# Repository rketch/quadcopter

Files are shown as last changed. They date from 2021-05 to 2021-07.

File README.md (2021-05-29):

# When Pigs Fly: The Quadcopter Project
The hardware and firmware for a quadcopter were made in the UCSD class CSE 176e: Robotic System Design and Implementation with [@ThomasStuart](https://github.com/ThomasStuart)

## Video of the quadcopter (click on gif)
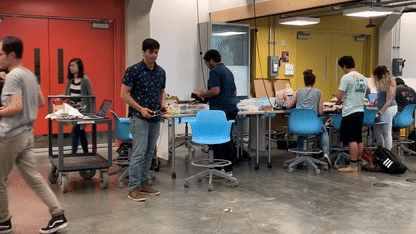
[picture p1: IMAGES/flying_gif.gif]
flying gif (https://www.youtube.com/watch?v=QjpneSxLLBc)


## Report on the design process
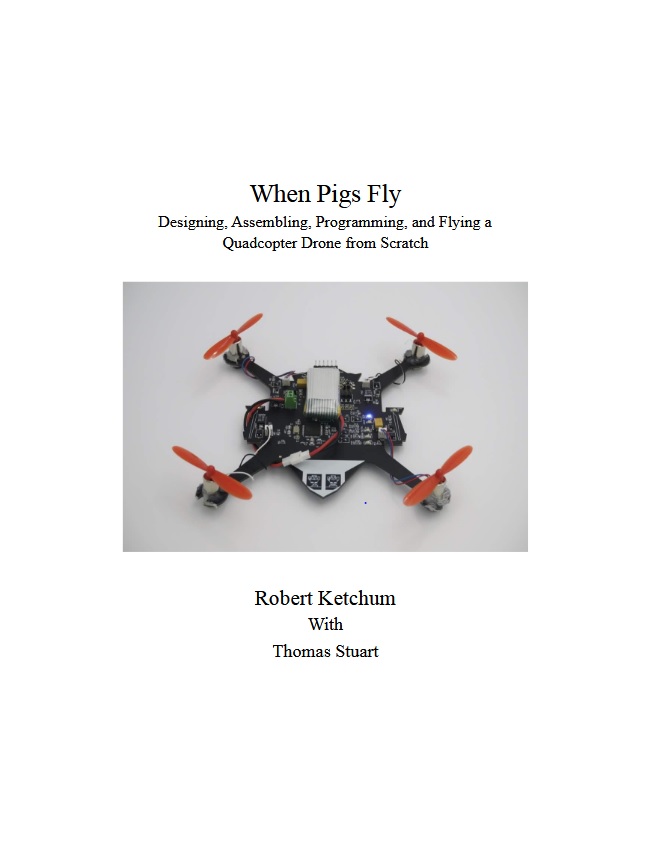
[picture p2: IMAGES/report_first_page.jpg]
photoshoot picture


## Various Pictures

Assembled quadcopter
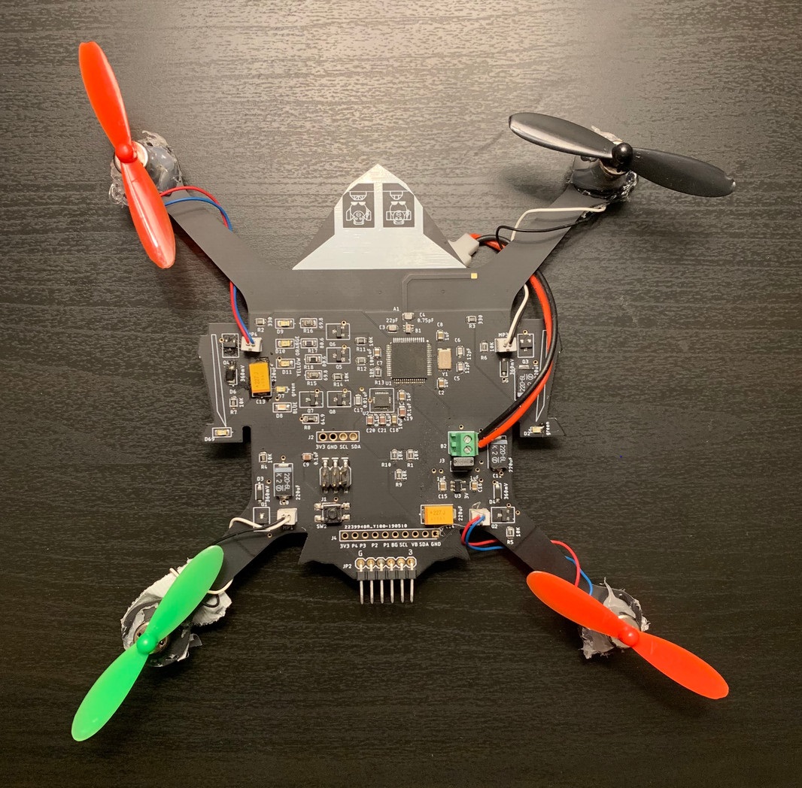
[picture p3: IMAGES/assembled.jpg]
assembled


Four bladed propellers with IMU breakout board
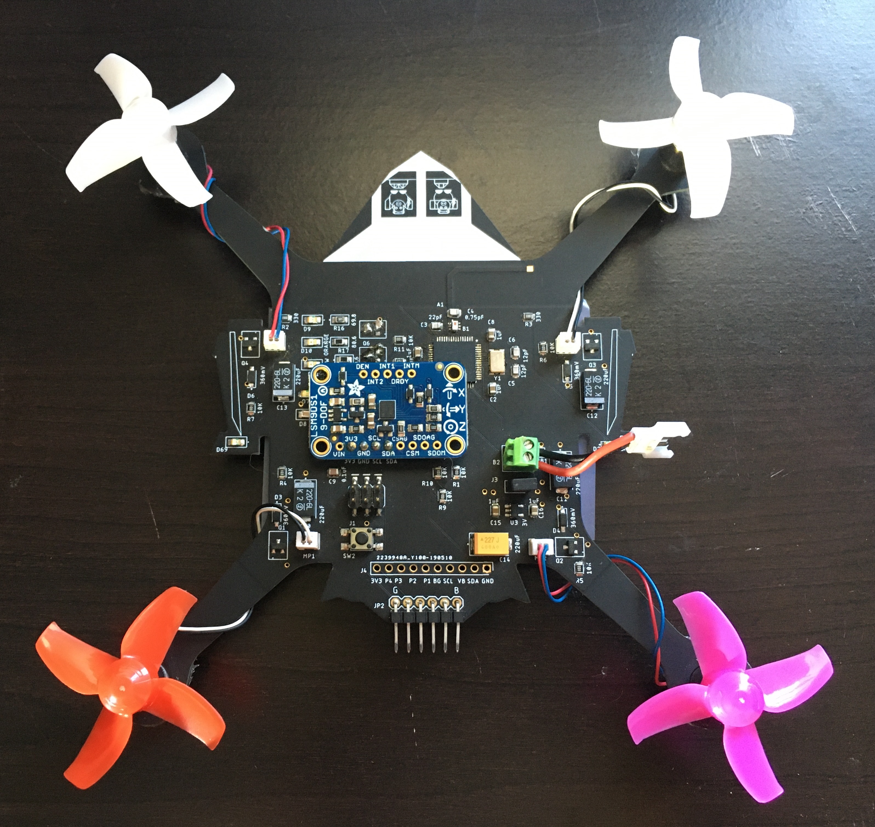
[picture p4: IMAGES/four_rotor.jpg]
four rotor


Remote PID control system tuning menu
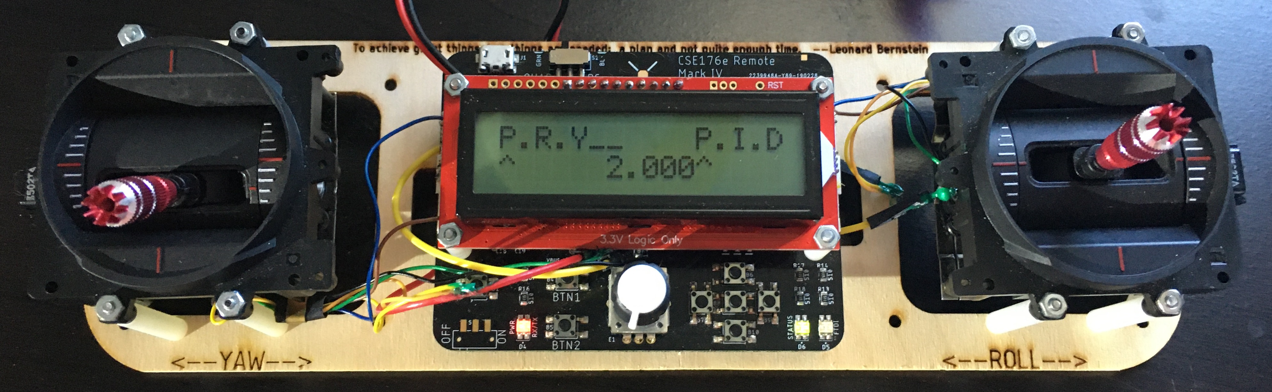
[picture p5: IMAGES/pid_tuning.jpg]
remote PID


Remote trim tuning menu
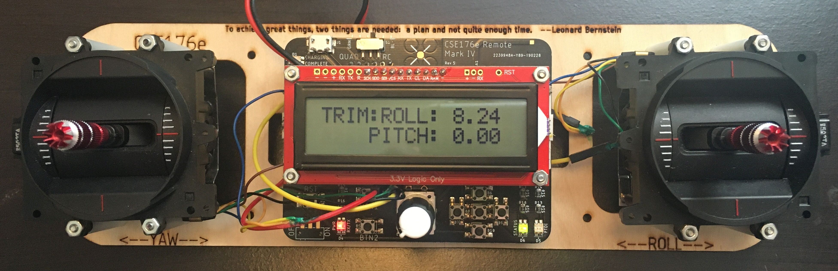
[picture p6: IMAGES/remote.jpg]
remote trim


Quadcopter orientation angles
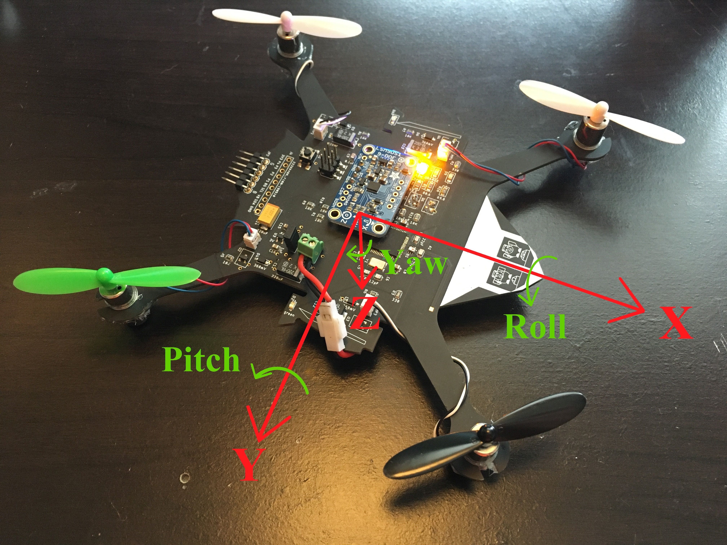
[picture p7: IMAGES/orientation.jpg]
orientation


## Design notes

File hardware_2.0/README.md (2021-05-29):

# EAGLE schematic and Board Files
These were updated in version 2.0 to fix wiring issues from the rainbow LED FETs to the microcontroller pins.

Created by @rketch and @ThomasStuart with continued updates and revisions by @rketch.

Libraries created by @stevenjswanson.

## Schematic
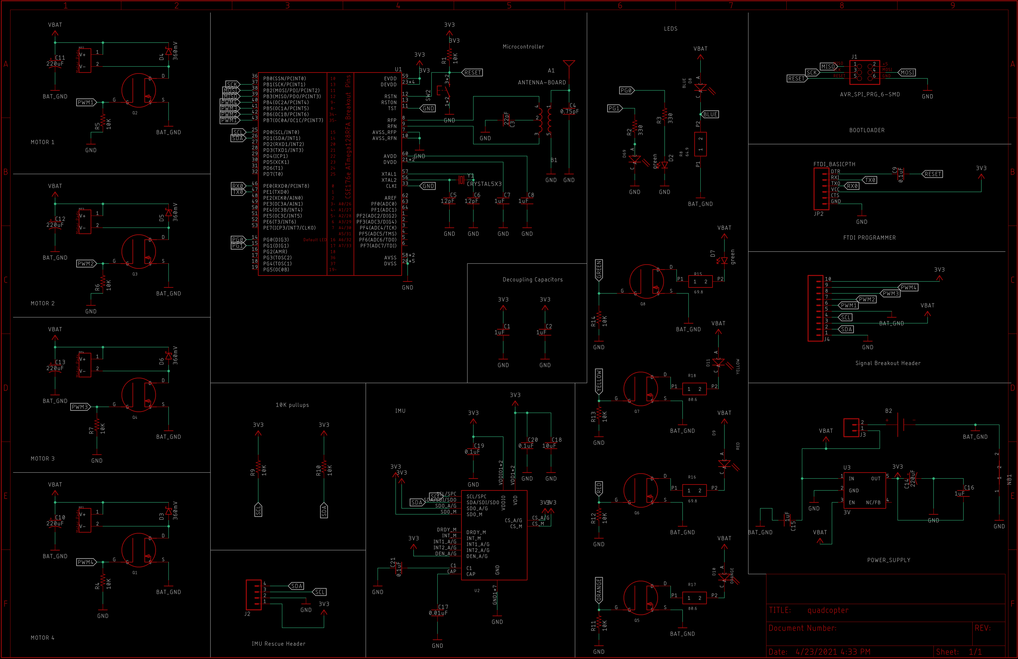
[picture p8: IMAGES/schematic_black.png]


## Layout
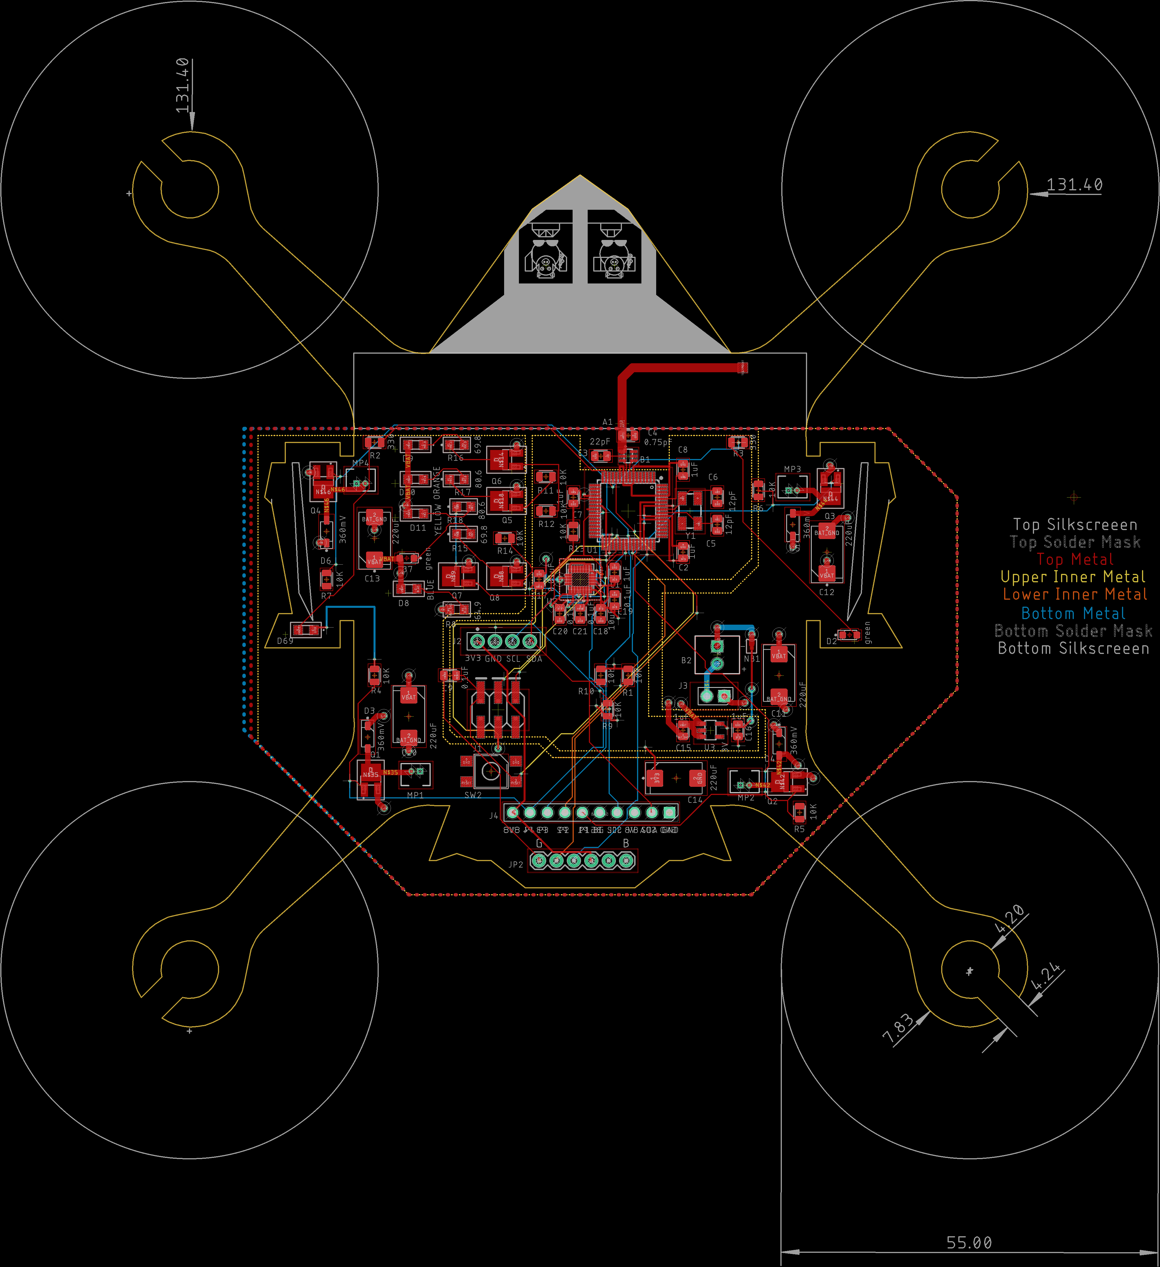
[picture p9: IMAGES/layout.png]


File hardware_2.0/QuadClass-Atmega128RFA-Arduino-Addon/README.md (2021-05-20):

# Arduino Board definitions for the ATmega128RFA1-based boards

This folder should be added to a *hardware* directory within your Arduino sketchbook. Normally the sketchbook will install to your documents/Arduino folder. If a *hardware* folder isn't already there, make it.

This directory contains a *boards.txt* file which defines how Arduino will handle ATmega128RFA1-based boards for the Quadcopter Class, and adds a selectable option under the *Tools > Board* menu. When you open the Arduino ID (close and reopen if it's already open), this option should be added to the menu.

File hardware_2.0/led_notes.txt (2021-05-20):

We have a total of 5 added LEDs.

Our blue LED D8 will be powered by the battery at 4.2 V. It is always on.
forward voltage: 2.9 V
Current limiting resistor: 64.9 ohms
LED current: 0.02 A

Our green LED D7 will be powered by the battery at 4.2 V. It wired to a MOSFET to blink at a programmed throttle position.
forward voltage: 2.1 V
Current limiting resistor: 69.8 ohms
LED current: 0.03 A

Our yellow LED D11 will be powered by the battery at 4.2 V. It wired to a MOSFET to blink at a programmed throttle position.
forward voltage: 1.85 V
Current limiting resistor: 80.6 ohms
LED current: 0.029 A

Our orange LED D10 will be powered by the battery at 4.2 V. It wired to a MOSFET to blink at a programmed throttle position.
forward voltage: 1.8 V
Current limiting resistor: 80.6 ohms
LED current: 0.03 A

Our red LED D9 will be powered by the battery at 4.2 V. It wired to a MOSFET to blink at a programmed throttle position.
forward voltage: 2.0 V
Current limiting resistor: 69.8 ohms
LED current: 0.032 A

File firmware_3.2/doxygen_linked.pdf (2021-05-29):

## Quadcopter

3.2

Generated by Doxygen 1.8.16

i

1 Quadcopter | 1
2 File Index | 3
3 File Documentation | 5

Generated by Doxygen

ii

iii

Index | 27

# Chapter 1

# Quadcopter

## 1.1 Description

The C++ Arduino firmware for a quadcopter made as part of UCSD class CSE 176e

## 1.2 Hardware

Custom PCB utilizing the ATmega128RFA1.

- Quadcopter hardware by Thomas Stuart and Robert Ketchum. Documentation and EAGLE board files available here: https://github.com/rketch/quadcopter
- Remote PCB made by UCSD Professor Steven Swanson.

## 1.3 Libraries

All libraries available at: https://github.com/rketch/quadcopter

- Wire

– Arduino I2C

- Arduino_LSM9DS1

– Onboard IMU for quadcopter orientation.

- Adafruit_Simple_AHRS

– Attitude and heading reference system for LSM

- radio

– Radio library. Modified to include data structure sent via radio

- quad_remote

– Custom CSE 176e library for the remote

- EEPROM

– To save PID and trim calibration values to Non-volatile memory

- RotaryEncoder

– To use the knob and button

### 2 Quadcopter

## 1.4 Authors

Created by Thomas Stuart and Robert Ketchum, April 2019. Modified by Robert Ketchum, May 2021.

# Chapter 2

# File Index

## 2.1 File List

Here is a list of all files with brief descriptions:

### 4 File Index

# Chapter 3

# File Documentation

## 3.1 quad_firmware/quad_firmware.ino File Reference

#include "radio.h"

#include <Wire.h>

#include <Adafruit_Simple_AHRS.h> #include <Adafruit_LSM9DS1.h>

Macros

- #define RADIO_CH 17

Radio Channel.
- #define M1 35

Pin 35 is mapped to motor 1.
- #define M2 34

Pin 34 is mapped to motor 2.
- #define M3 8

Pin 8 is mapped to motor 3.
- #define M4 9

Pin 9 is mapped to motor 4.
- #define FILT_RATIO 0.91

Complementary filter ratio for a time constant of 10 Hz = 0.91.
- #define MS_TO_S 1000

Conversion ratio.
- #define NEUTRAL_PITCH 43

Neutral pitch gimbal position.
- #define NEUTRAL_ROLL 60

Neutral roll gimbal position.
- #define NEUTRAL_YAW 60

Neutral yaw gimbal position.
- #define MAX_ANGLE_FROM_NEUTRAL 10

Maximum pitch or roll from neutral.
- #define MAX_TRIM_ANGLE 30

Maximum pitch or roll trim angle.
- #define YAW_MAX_ANG_VEL 60

Maximum yaw angular velocity (deg/sec)
- #define TRIM_HISTORY 3

Number of median filtered trim values.

### 6 File Documentation

Functions

- Adafruit_Simple_AHRS ahrs & lsm (), &lsm.getMag(), &lsm.getGyro()
- void setupLSM ()
- void setup ()
- void loop ()
- void verifyRadioData ()
- void ComplimentaryFilter (double dt)
- void PID (double dt)
- void findGimbalOffsets ()
- void findTrimOffsets ()
- float median (float medArray[ ], int n)
- void sort (float unsortedArray[ ], int n)
- void calibrateAccelerometer ()
- void mixer ()
- void initializeMotors ()
- void disableMotors ()
- void engageMotors ()

Variables

- unsigned long time

Current time since start.
- unsigned int last = millis()

Last loop time since start.
- double timeDiff = 0.000000

Implemented in complementary filter and controller.
- struct Data dataFromRemote

Data structure received over radio.
- bool resetFlag = false

For zeroing off orientation offset when armed.
- quad_data_t orientation

Data structure with quadcopter orientation.
- float accHistoryArr [3][2]

pitch, roll accelerometer reading history
- float accHistoryArrCopy [3]

For median filter.
- float rawGyro [2]

Raw gyro pitch, roll rate.
- float gyroAngle [2]

Integrated gyro angles.
- float rawAcc [2]

Raw accelerometer angles.
- float filteredAngle [2]

Complementary filtered angle.
- float filtGyroAngle [2]

Partially filtered gyro angle.
- float filtAccelAngle [2]

Partially filtered accelerometer angle.
- float gyroAngleStepBack [2]

Previous time step filtered gyroscope angle. Needed for complementary filter.

3.1 quad_firmware/quad_firmware.ino File Reference | 7
- float angleOffset [2]

Accelerometer offset from neutral. Measured when armed.
- float trimAngle [2]

Trimm offsets.
- float trimHistoryArr [3][4]

Pitch, roll trim floats.
- float trimHistoryArrCopy [3]

Trim History for median filter.
- float medOutTrimArray [4]

Pitch, roll median filter outputs.
- float PID_output [3]

PID output.
- float remoteSetAngle [3]

Set angle.
- float currentAngle [3]

Current quadcopter angle.
- float error [3]

Error angle.
- float errorSum [3]

Integrated error.
- float lastError [3]

previous error (for derivative)
- float MotorValue [4]

Implemented motor thrust variables.
- Adafruit_LSM9DS1 lsm = Adafruit_LSM9DS1()

Create LSM9DS1 board instance.

### 3.1.1 Macro Definition Documentation

### 3.1.1.1 FILT_RATIO

#define FILT_RATIO 0.91

Complementary filter ratio for a time constant of 10 Hz = 0.91.

### 3.1.1.2 M1

#define M1 35

Pin 35 is mapped to motor 1.

### 8 File Documentation

### 3.1.1.3 M2

#define M2 34

Pin 34 is mapped to motor 2.

### 3.1.1.4 M3

#define M3 8

Pin 8 is mapped to motor 3.

### 3.1.1.5 M4

#define M4 9

Pin 9 is mapped to motor 4.

### 3.1.1.6 MAX_ANGLE_FROM_NEUTRAL

#define MAX_ANGLE_FROM_NEUTRAL 10

Maximum pitch or roll from neutral.

### 3.1.1.7 MAX_TRIM_ANGLE

#define MAX_TRIM_ANGLE 30

Maximum pitch or roll trim angle.

### 3.1.1.8 MS_TO_S

#define MS_TO_S 1000

Conversion ratio.

3.1 quad_firmware/quad_firmware.ino File Reference | 9

### 3.1.1.9 NEUTRAL_PITCH

#define NEUTRAL_PITCH 43

Neutral pitch gimbal position.

### 3.1.1.10 NEUTRAL_ROLL

#define NEUTRAL_ROLL 60

Neutral roll gimbal position.

### 3.1.1.11 NEUTRAL_YAW

#define NEUTRAL_YAW 60

Neutral yaw gimbal position.

### 3.1.1.12 RADIO_CH

#define RADIO_CH 17

Radio Channel.

### 3.1.1.13 TRIM_HISTORY

#define TRIM_HISTORY 3

Number of median filtered trim values.

### 3.1.1.14 YAW_MAX_ANG_VEL

#define YAW_MAX_ANG_VEL 60

Maximum yaw angular velocity (deg/sec)

### 3.1.2 Function Documentation

### 3.1.2.1 calibrateAccelerometer()

void calibrateAccelerometer ( )
Calculate the angle offset of the accelerometer

### 3.1.2.2 ComplimentaryFilter()

void ComplimentaryFilter (

double dt )
Combine the gyroscope and accelerometer to get an accurate heading of the quadcopter

### 10 File Documentation

Parameters

dt The time difference between calling the function (in ms)

### 3.1.2.3 disableMotors()

void disableMotors ( )

Ensure that the motors do not run when the quad is disarmed

### 3.1.2.4 engageMotors()

void engageMotors ( )

Write the motor commands to the respective motors

### 3.1.2.5 findGimbalOffsets()

void findGimbalOffsets ( )

Find the remote set angles from the gimbal positions

### 3.1.2.6 findTrimOffsets()

void findTrimOffsets ( )

Median the trim data and convert to a float angle.

### 3.1.2.7 initializeMotors()

void initializeMotors ( )

Initialize motor pins

### 3.1.2.8 loop()

void loop ( )

Loop forever. Receive radio data, find current quadcopter orientation, compute control system values, find current throttle corrections,write throttle values to motors if armed.

### 3.1.2.9 lsm()

Adafruit_Simple_AHRS ahrs& lsm ( ) &

### 3.1.2.10 median()

float median (

float medArray[ ],

int n )

Find the middle value of three raw inputs to filter out pertubations. Thanks geeksforgeeks

3.1 quad_firmware/quad_firmware.ino File Reference | 11

Parameters

medArray | An array containing the last n sensed values
n | The length of medArray

Returns

The median value

### 3.1.2.11 mixer()

void mixer ( )

Mix the user throttle value and the PID controller output

### 3.1.2.12 PID()

void PID (

double dt )

Utilize PID controller to ensure stable quadcopter flight

Parameters

dt The time difference between calling the function (in ms)

### 3.1.2.13 setup()

void setup ( )

Setup the quadcopter by initializing the radio, motors, IMU registers, and start clock

### 3.1.2.14 setupLSM()

void setupLSM ( )

set up our instance of the sensor with the wanted register values

### 3.1.2.15 sort()

void sort (

float unsortedArray[ ],

int n )

Sort an array into increasing numerical values. Thanks tsbrownie on youtube.

### 12 File Documentation

Parameters

unsortedArray | An array containing the last n sensed values
n | The length of medianFinder

### 3.1.2.16 verifyRadioData()

void verifyRadioData ( )

Read radio data received from the remote. If it is verified, save the data in a structure

### 3.1.3 Variable Documentation

### 3.1.3.1 accHistoryArr

float accHistoryArr[3][2]

pitch, roll accelerometer reading history

### 3.1.3.2 accHistoryArrCopy

float accHistoryArrCopy[3]

For median filter.

### 3.1.3.3 angleOffset

float angleOffset[2]

Accelerometer offset from neutral. Measured when armed.

### 3.1.3.4 currentAngle

float currentAngle[3]

Current quadcopter angle.

3.1 quad_firmware/quad_firmware.ino File Reference | 13

### 3.1.3.5 dataFromRemote

struct Data dataFromRemote

Data structure received over radio.

### 3.1.3.6 error

float error[3]

Error angle.

### 3.1.3.7 errorSum

float errorSum[3]

Integrated error.

### 3.1.3.8 filtAccelAngle

float filtAccelAngle[2]

Partially filtered accelerometer angle.

### 3.1.3.9 filteredAngle

float filteredAngle[2]

Complementary filtered angle.

### 3.1.3.10 filtGyroAngle

float filtGyroAngle[2]

Partially filtered gyro angle.

### 14 File Documentation

### 3.1.3.11 gyroAngle

float gyroAngle[2]

Integrated gyro angles.

### 3.1.3.12 gyroAngleStepBack

float gyroAngleStepBack[2]

Previous time step filtered gyroscope angle. Needed for complementary filter.

### 3.1.3.13 last

unsigned int last = millis()

Last loop time since start.

### 3.1.3.14 lastError

float lastError[3]

previous error (for derivative)

### 3.1.3.15 lsm

Adafruit_LSM9DS1 lsm = Adafruit_LSM9DS1()

Create LSM9DS1 board instance.

### 3.1.3.16 medOutTrimArray

float medOutTrimArray[4]

Pitch, roll median filter outputs.

3.1 quad_firmware/quad_firmware.ino File Reference | 15

### 3.1.3.17 MotorValue

float MotorValue[4]

Implemented motor thrust variables.

### 3.1.3.18 orientation

quad_data_t orientation

Data structure with quadcopter orientation.

### 3.1.3.19 PID_output

float PID_output[3]

PID output.

### 3.1.3.20 rawAcc

float rawAcc[2]

Raw accelerometer angles.

### 3.1.3.21 rawGyro

float rawGyro[2]

Raw gyro pitch, roll rate.

### 3.1.3.22 remoteSetAngle

float remoteSetAngle[3]

Set angle.

### 16 File Documentation

### 3.1.3.23 resetFlag

bool resetFlag = false

For zeroing off orientation offset when armed.

### 3.1.3.24 time

unsigned long time

Current time since start.

### 3.1.3.25 timeDiff

double timeDiff = 0.000000

Implemented in complementary filter and controller.

### 3.1.3.26 trimAngle

float trimAngle[2]

Trimm offsets.

### 3.1.3.27 trimHistoryArr

float trimHistoryArr[3][4]

Pitch, roll trim floats.

### 3.1.3.28 trimHistoryArrCopy

float trimHistoryArrCopy[3]

Trim History for median filter.

3.2 remote_firmware/remote_firmware.ino File Reference | 17

## 3.2 remote_firmware/remote_firmware.ino File Reference

#include "quad_remote.h"

#include "radio.h"

#include <EEPROM.h>

#include <RotaryEncoder.h>

Macros

- #define RADIO_CH 17

Radio Channel.
- #define MAX_TRIM_ANGLE 30

Maximum trim angle.
- #define TRIM_INCREMENT 10

Increment by which trim is changed on remote.

Functions

- void knobPressed (bool)
- void knobsUpdate ()
- int calculateColPos (int, bool)
- void updateDisplayPIDElementChange ()
- void converToDecimalsBeforeSend ()
- float castIntPairToDecimal (int, int)
- void readPIDArrayFromEeprom (int)
- void writePIDToEeprom ()
- void writeGimbalsToEeprom ()
- void setup ()
- void loop ()
- void PIDTuningState ()
- void TrimTuningState ()
- void updateDisplayTrimElementChange ()
- void calculateTuningValues ()
- void readAndMapGimbals ()
- void isInArmState (Data &d)
- void calibrate ()
- void updateDisplayPIDNumChange ()
- void eepromRead ()
- void readTrimFromEeprom (int EepromAddress)
- void resetCoefficientValuesAndSigns ()
- void initializeButtonPins ()

### 18 File Documentation

Variables

- struct Data remoteToQuadData

Structure for radio data. Struct "Data" initialized in radio.h.
- int gimbalRawValues [4]

Values read by gimbal. Nominally 0 - 1024 but constrained by the potentiometer.
- int lowestGimbalValueReadSoFar [4] = { 0, 0, 0, 0}

lowest value possible by analog stick gimbal
- int largestGimbalValueReadSoFar [4] = {303, 318, 320, 306}

highest value possible by analog stick gimbal
- int saveLargestGimbalValuesSoFar [12]

255 + 255 + 255 = 765 is the highest save value with EEPROM for gimbal
- bool knob_btn = 0

Whether the knob button is pressed.
- bool armToken = true

State variable for armed mode.
- bool isInTrimMode = false

State variable for trim mode.
- int cpa [3][6]

Coefficients Properties Array for displaying and storing PID coefficients for pitch, yaw, roll. 3 rows, 6 columns.
- int sign [9] = {1,1,1, 1,1,1, 1,1,1}

Sign of PID tuning coefficients for storing via EEPROM.
- int PIDpos = 0

PID value being tuned currently.
- bool changeLeft = 1

Keeps track of whether we are tuning whole integer or decimal PID value.
- int row = 0

LCD screen row to write to.
- int col = 0

LCD screen column to write to.
- float trimAngle [2]

Trim pitch and roll angles.
- String top = ""

Initialize string to print on top row of LCD screen for PID tuning.
- int colPosStart [3]

What column we are writing to LCD screen for PID tuning.
- bool knob_token = false

trim or PID tuning variable
- int timesOverflowed = 0

Keeps track of times an integer has overflowed for EEPROM writing.

### 3.2.1 Macro Definition Documentation

### 3.2.1.1 MAX_TRIM_ANGLE

#define MAX_TRIM_ANGLE 30

Maximum trim angle.

3.2 remote_firmware/remote_firmware.ino File Reference | 19

### 3.2.1.2 RADIO_CH

#define RADIO_CH 17

Radio Channel.

### 3.2.1.3 TRIM_INCREMENT

#define TRIM_INCREMENT 10

Increment by which trim is changed on remote.

### 3.2.2 Function Documentation

### 3.2.2.1 calculateColPos()

int calculateColPos (

int pidPos,

bool tuningWholeInteger )

Determines which cpa array column value we wish to edit

Parameters

pidPos | 0->2: Pitch, Roll, Yaw
tuningWholeInteger | Whether we are tuning an integer or decimal

### 3.2.2.2 calculateTuningValues()

void calculateTuningValues ( )

Calculates the tuning values displayed and sent to the quad (float) from the values saved to EEPROM (int)

### 3.2.2.3 calibrate()

void calibrate ( )

Calibrates the gimbals and call function writeGimbalsToEeprom to save the new values. Scripted and hardcoded out of necessity.

### 20 File Documentation

### 3.2.2.4 castIntPairToDecimal()

float castIntPairToDecimal (

int left_int,

int right_int )

Takes the separated PID integers displayed on the LCD and combines them into one float value

Parameters

left_int | integer in the ones place on the LCD screen
right_int | integer in the decimal place on the LCD screen

Returns

castedPIDValue float value which may be used in computation

### 3.2.2.5 converToDecimalsBeforeSend()

void converToDecimalsBeforeSend ( )

Takes the PID user input as displayed on the LCD (as unsigned integers) and saves it in the structure "remoteTo←-QuadData" (as floats), which will be sent over radio to the quadcopter. It also stores the sign of the PID values for EEPROM saving

### 3.2.2.6 eepromRead()

void eepromRead ( )

Read the values stored in EEPROM and store in a data structure

### 3.2.2.7 initializeButtonPins()

void initializeButtonPins ( )

Initializes all buttons on the remote

### 3.2.2.8 isInArmState()

void isInArmState (

Data & d )

Arms the quadcopter if the gimbals are down and out

3.2 remote_firmware/remote_firmware.ino File Reference | 21

Parameters

&d pointer to the the data structure containing throttle being sent via radio to the quadcopter

### 3.2.2.9 knobPressed()

void knobPressed (

bool down )

Resets the current displayed PID or trim values

Parameters

down the boolean which stores whether the knob is pressed

### 3.2.2.10 knobsUpdate()

void knobsUpdate ( )

Updates the stored knob value so that it agrees with the stored PID value displayed on the LCD screen

### 3.2.2.11 loop()

void loop ( )

Loop endlessly. Read gimbal positions, determine if quadcopter should be armed, determine which LCD tuning state the remote should be in, determine whether the user is inputing commands, and send data structure to quadcopter over radio.

### 3.2.2.12 PIDTuningState()

void PIDTuningState ( )

This function serves as a state machine. It is called when the remote is in the PID editing state

### 3.2.2.13 readAndMapGimbals()

void readAndMapGimbals ( )

Reads the analog gimbal positions and map to a value which may be sent over radio

### 3.2.2.14 readPIDArrayFromEeprom()

void readPIDArrayFromEeprom (

int currentEEPROMAddressNumber )

Reads the PID values stored in EEPROM

### 22 File Documentation

Parameters

currentEEPROMAdressNumber necessary to read correct data

### 3.2.2.15 readTrimFromEeprom()

void readTrimFromEeprom (

int EepromAddress )

Reads the trim values stored in EEPROM

Parameters

EepromAddress eeprom address to read correct data (should be at 43)

### 3.2.2.16 resetCoefficientValuesAndSigns()

void resetCoefficientValuesAndSigns ( )

Resets all PID coefficients.

### 3.2.2.17 setup()

void setup ( )

Setup the remote firmware by initializing radio, gimbal pins, LCD screen, knobs and buttons, and reading PID and trim values from EEPROM.

### 3.2.2.18 TrimTuningState()

void TrimTuningState ( )

This function serves as a state machine. It is called when the remote is in the Trim editing state

### 3.2.2.19 updateDisplayPIDElementChange()

void updateDisplayPIDElementChange ( )

Updates the entire LCD screen to the PID state. It should be called when an element changes on the LCD screen. For example: arming the controller or changing which pitch, roll, or yaw PID value is being tuned.

3.2 remote_firmware/remote_firmware.ino File Reference | 23

### 3.2.2.20 updateDisplayPIDNumChange()

void updateDisplayPIDNumChange ( )

Updates the numbers being displayed currently on the LCD screen. It should be called when a number changes.

### 3.2.2.21 updateDisplayTrimElementChange()

void updateDisplayTrimElementChange ( )

Updates the entire LCD screen to the tuning state. It should be called when an element changes on the LCD screen.

### 3.2.2.22 writeGimbalsToEeprom()

void writeGimbalsToEeprom ( )

Saves the calibrated gimbal values to the microcontroller's EEPROM

### 3.2.2.23 writePIDToEeprom()

void writePIDToEeprom ( )

Saves the PID and trim coefficients to the microcontroller's EEPROM

### 3.2.3 Variable Documentation

### 3.2.3.1 armToken

bool armToken = true

State variable for armed mode.

### 3.2.3.2 changeLeft

bool changeLeft = 1

Keeps track of whether we are tuning whole integer or decimal PID value.

### 24 File Documentation

### 3.2.3.3 col

int col = 0

LCD screen column to write to.

### 3.2.3.4 colPosStart

int colPosStart[3]

What column we are writing to LCD screen for PID tuning.

### 3.2.3.5 cpa

int cpa[3][6]

Coefficients Properties Array for displaying and storing PID coefficients for pitch, yaw, roll. 3 rows, 6 columns.

### 3.2.3.6 gimbalRawValues

int gimbalRawValues[4]

Values read by gimbal. Nominally 0 - 1024 but constrained by the potentiometer.

### 3.2.3.7 isInTrimMode

bool isInTrimMode = false

State variable for trim mode.

### 3.2.3.8 knob_btn

bool knob_btn = 0

Whether the knob button is pressed.

3.2 remote_firmware/remote_firmware.ino File Reference | 25

### 3.2.3.9 knob_token

bool knob_token = false

trim or PID tuning variable

### 3.2.3.10 largestGimbalValueReadSoFar

int largestGimbalValueReadSoFar[4] = {303, 318, 320, 306}

highest value possible by analog stick gimbal

### 3.2.3.11 lowestGimbalValueReadSoFar

int lowestGimbalValueReadSoFar[4] = { 0, 0, 0, 0}

lowest value possible by analog stick gimbal

### 3.2.3.12 PIDpos

int PIDpos = 0

PID value being tuned currently.

### 3.2.3.13 remoteToQuadData

struct Data remoteToQuadData

Structure for radio data. Struct "Data" initialized in radio.h.

### 3.2.3.14 row

int row = 0

LCD screen row to write to.

### 26 File Documentation

### 3.2.3.15 saveLargestGimbalValuesSoFar

int saveLargestGimbalValuesSoFar[12]

255 + 255 + 255 = 765 is the highest save value with EEPROM for gimbal

### 3.2.3.16 sign

int sign[9] = {1,1,1, 1,1,1, 1,1,1}

Sign of PID tuning coefficients for storing via EEPROM.

### 3.2.3.17 timesOverflowed

int timesOverflowed = 0

Keeps track of times an integer has overflowed for EEPROM writing.

### 3.2.3.18 top

String top = ""

Initialize string to print on top row of LCD screen for PID tuning.

### 3.2.3.19 trimAngle

float trimAngle[2]

Trim pitch and roll angles.

# Index

accHistoryArr
quad_firmware.ino, 12
accHistoryArrCopy
quad_firmware.ino, 12
angleOffset
quad_firmware.ino, 12
armToken
remote_firmware.ino, 23

calculateColPos
remote_firmware.ino, 19
calculateTuningValues
remote_firmware.ino, 19
calibrate
remote_firmware.ino, 19
calibrateAccelerometer
quad_firmware.ino,
9
castIntPairToDecimal
remote_firmware.ino, 19
changeLeft
remote_firmware.ino, 23
col
remote_firmware.ino, 23
colPosStart
remote_firmware.ino, 24
ComplimentaryFilter
quad_firmware.ino,
9
converToDecimalsBeforeSend remote_firmware.ino, 20
cpa
remote_firmware.ino, 24
currentAngle
quad_firmware.ino, 12

dataFromRemote
quad_firmware.ino, 12
disableMotors
quad_firmware.ino, 10

eepromRead
remote_firmware.ino, 20
engageMotors
quad_firmware.ino, 10
error
quad_firmware.ino, 13
errorSum
quad_firmware.ino, 13

FILT_RATIO
quad_firmware.ino,
7

filtAccelAngle
quad_firmware.ino, 13
filteredAngle
quad_firmware.ino, 13
filtGyroAngle
quad_firmware.ino, 13
findGimbalOffsets
quad_firmware.ino, 10
findTrimOffsets
quad_firmware.ino, 10

gimbalRawValues
remote_firmware.ino, 24
gyroAngle
quad_firmware.ino, 13
gyroAngleStepBack
quad_firmware.ino, 14

initializeButtonPins
remote_firmware.ino, 20
initializeMotors
quad_firmware.ino, 10
isInArmState
remote_firmware.ino, 20
isInTrimMode
remote_firmware.ino, 24

knob_btn
remote_firmware.ino, 24
knob_token
remote_firmware.ino, 24
knobPressed
remote_firmware.ino, 21
knobsUpdate
remote_firmware.ino, 21

largestGimbalValueReadSoFar remote_firmware.ino, 25
last
quad_firmware.ino, 14
lastError
quad_firmware.ino, 14
loop
quad_firmware.ino, 10
remote_firmware.ino, 21
lowestGimbalValueReadSoFar remote_firmware.ino, 25
lsm
quad_firmware.ino, 10
, 14

M1

### 28 INDEX

quad_firmware.ino, 7
M2
quad_firmware.ino, 7
M3
quad_firmware.ino, 8
M4
quad_firmware.ino, 8
MAX_ANGLE_FROM_NEUTRAL
quad_firmware.ino, 8
MAX_TRIM_ANGLE
quad_firmware.ino, 8
remote_firmware.ino, 18
median
quad_firmware.ino, 10
medOutTrimArray
quad_firmware.ino, 14
mixer
quad_firmware.ino, 11
MotorValue
quad_firmware.ino, 14
MS_TO_S
quad_firmware.ino, 8

NEUTRAL_PITCH
quad_firmware.ino, 8
NEUTRAL_ROLL
quad_firmware.ino, 9
NEUTRAL_YAW
quad_firmware.ino, 9

orientation
quad_firmware.ino, 15

PID
quad_firmware.ino, 11
PID_output
quad_firmware.ino, 15
PIDpos
remote_firmware.ino, 25
PIDTuningState
remote_firmware.ino, 21

quad_firmware.ino
accHistoryArr, 12
accHistoryArrCopy, 12
angleOffset, 12
calibrateAccelerometer, 9
ComplimentaryFilter, 9
currentAngle, 12
dataFromRemote, 12
disableMotors, 10
engageMotors, 10
error, 13
errorSum, 13
FILT_RATIO, 7
filtAccelAngle, 13
filteredAngle, 13
filtGyroAngle, 13
findGimbalOffsets, 10

findTrimOffsets, 10
gyroAngle, 13
gyroAngleStepBack, 14
initializeMotors, 10
last, 14
lastError, 14
loop, 10
lsm, 10, 14
M1, 7
M2, 7
M3, 8
M4, 8
MAX_ANGLE_FROM_NEUTRAL, 8
MAX_TRIM_ANGLE, 8
median, 10
medOutTrimArray, 14
mixer, 11
MotorValue, 14
MS_TO_S, 8
NEUTRAL_PITCH, 8
NEUTRAL_ROLL, 9
NEUTRAL_YAW, 9
orientation, 15
PID, 11
PID_output, 15
RADIO_CH, 9
rawAcc, 15
rawGyro, 15
remoteSetAngle, 15
resetFlag, 15
setup, 11
setupLSM, 11
sort, 11
time, 16
timeDiff, 16
TRIM_HISTORY, 9
trimAngle, 16
trimHistoryArr, 16
trimHistoryArrCopy, 16
verifyRadioData, 12
YAW_MAX_ANG_VEL, 9
quad_firmware/quad_firmware.ino, 5

RADIO_CH
quad_firmware.ino, 9
remote_firmware.ino, 18
rawAcc
quad_firmware.ino, 15
rawGyro
quad_firmware.ino, 15
readAndMapGimbals
remote_firmware.ino, 21
readPIDArrayFromEeprom
remote_firmware.ino, 21
readTrimFromEeprom
remote_firmware.ino, 22
remote_firmware.ino
armToken, 23
calculateColPos, 19

INDEX | 29

calculateTuningValues, 19
calibrate, 19
castIntPairToDecimal, 19
changeLeft, 23
col, 23
colPosStart, 24
converToDecimalsBeforeSend, 20 cpa, 24
eepromRead, 20
gimbalRawValues, 24
initializeButtonPins, 20
isInArmState, 20
isInTrimMode, 24
knob_btn, 24
knob_token, 24
knobPressed, 21
knobsUpdate, 21
largestGimbalValueReadSoFar, 25 loop, 21
lowestGimbalValueReadSoFar, 25 MAX_TRIM_ANGLE, 18
PIDpos, 25
PIDTuningState, 21
RADIO_CH, 18
readAndMapGimbals, 21
readPIDArrayFromEeprom, 21 readTrimFromEeprom, 22
remoteToQuadData, 25
resetCoefficientValuesAndSigns, 22 row, 25
saveLargestGimbalValuesSoFar, 25 setup, 22
sign, 26
timesOverflowed, 26
top, 26
TRIM_INCREMENT, 19
trimAngle, 26
TrimTuningState, 22
updateDisplayPIDElementChange, 22 updateDisplayPIDNumChange, 22 updateDisplayTrimElementChange, 23 writeGimbalsToEeprom, 23
writePIDToEeprom, 23
remote_firmware/remote_firmware.ino, 17 remoteSetAngle
quad_firmware.ino, 15
remoteToQuadData
remote_firmware.ino, 25
resetCoefficientValuesAndSigns remote_firmware.ino, 22
resetFlag
quad_firmware.ino, 15
row
remote_firmware.ino, 25

saveLargestGimbalValuesSoFar remote_firmware.ino, 25
setup
quad_firmware.ino, 11

remote_firmware.ino, 22
setupLSM
quad_firmware.ino, 11
sign
remote_firmware.ino, 26
sort
quad_firmware.ino, 11

time
quad_firmware.ino, 16
timeDiff
quad_firmware.ino, 16
timesOverflowed
remote_firmware.ino, 26
top
remote_firmware.ino, 26
TRIM_HISTORY
quad_firmware.ino,
9
TRIM_INCREMENT
remote_firmware.ino, 19
trimAngle
quad_firmware.ino, 16
remote_firmware.ino, 26
trimHistoryArr
quad_firmware.ino, 16
trimHistoryArrCopy
quad_firmware.ino, 16
TrimTuningState
remote_firmware.ino, 22

updateDisplayPIDElementChange remote_firmware.ino, 22
updateDisplayPIDNumChange
remote_firmware.ino, 22
updateDisplayTrimElementChange remote_firmware.ino, 23

verifyRadioData
quad_firmware.ino, 12

writeGimbalsToEeprom
remote_firmware.ino, 23
writePIDToEeprom
remote_firmware.ino, 23

YAW_MAX_ANG_VEL
quad_firmware.ino,
9

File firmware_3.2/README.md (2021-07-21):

# Quadcopter and Remote Firmware

Updated to provide doxygen support in 3.2.

Created by @rketch and @ThomasStuart with continued updates and revisions by @rketch.

Libraries created by @stevenjswanson.

## Doxygen LaTeX Output
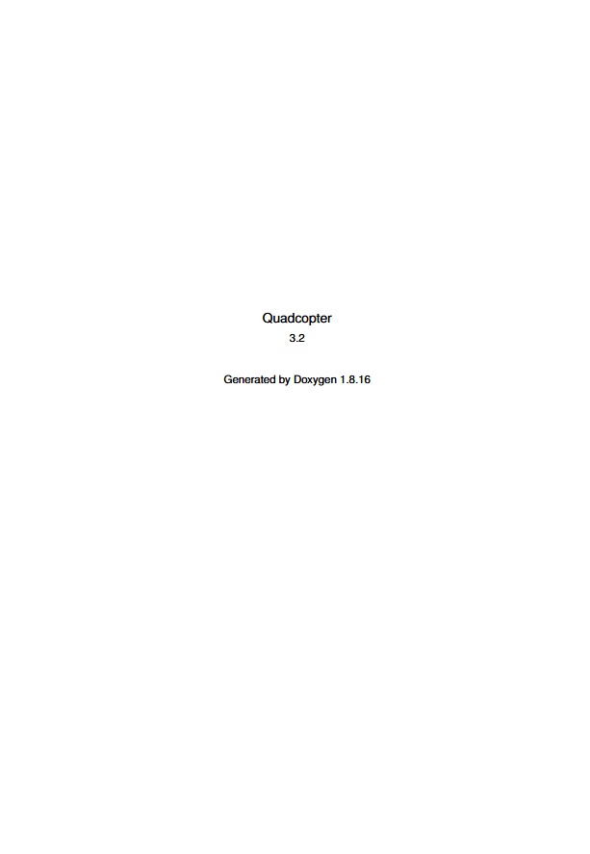
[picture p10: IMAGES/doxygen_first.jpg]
doxygen pdf


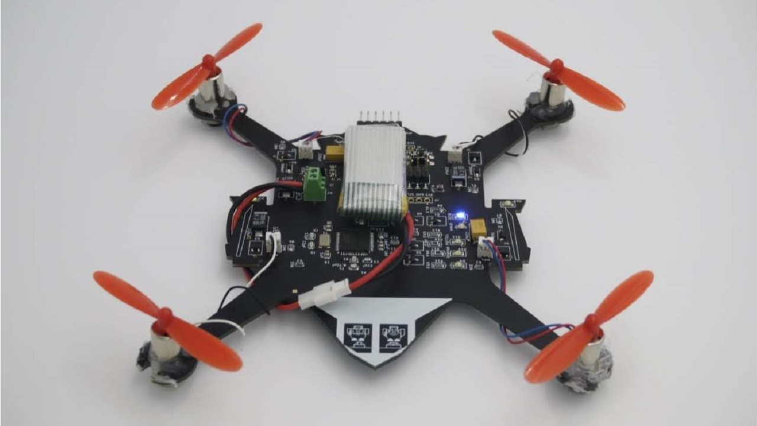
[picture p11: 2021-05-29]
IMAGES/photoshoot.jpg

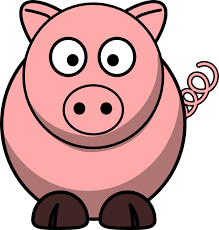
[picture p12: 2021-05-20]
IMAGES/pigEasy.png

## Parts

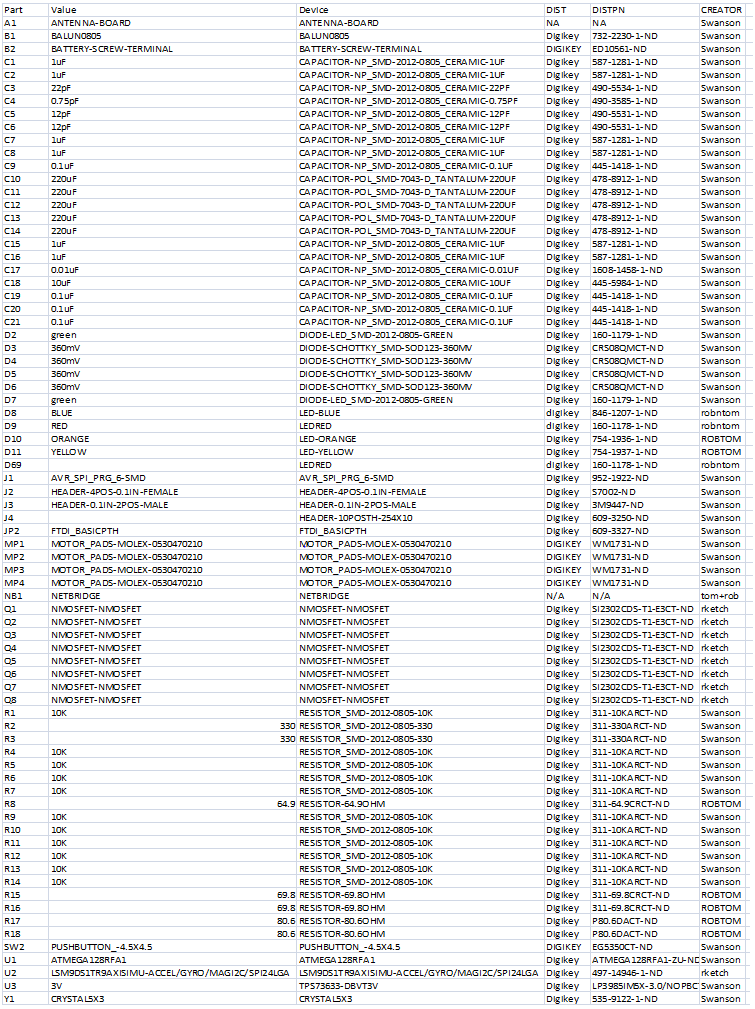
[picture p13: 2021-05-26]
IMAGES/BOM.png

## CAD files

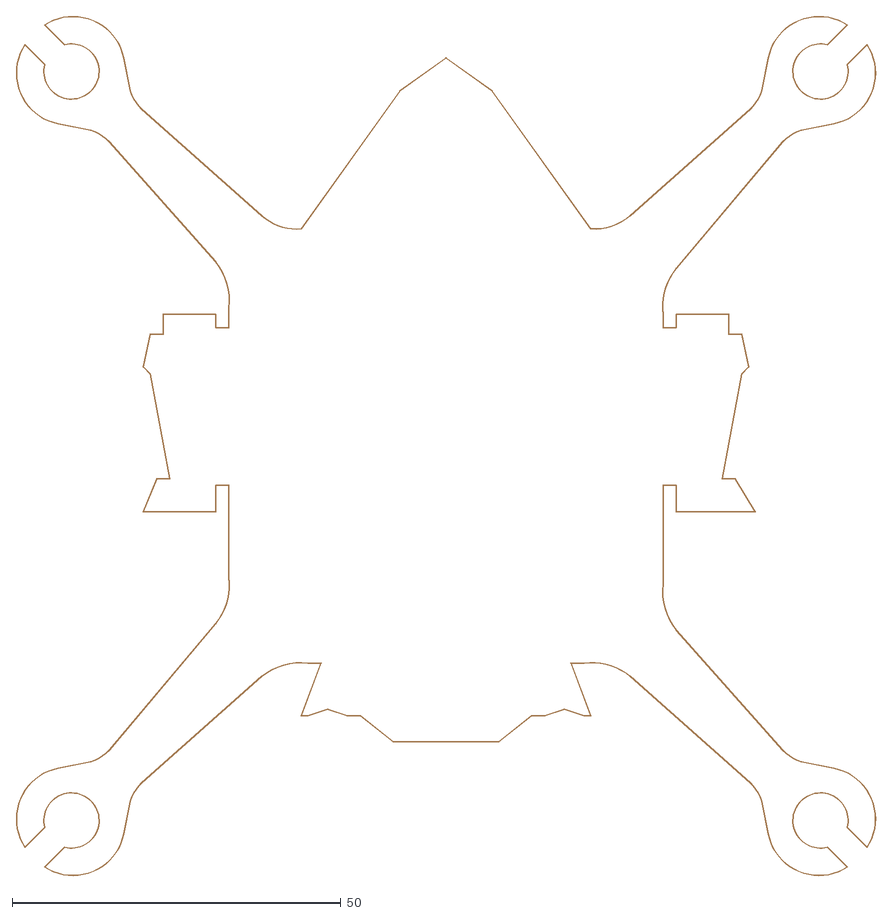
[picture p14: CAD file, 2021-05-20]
hardware_2.0/quadcopter.dxf
130.7 x 130.7

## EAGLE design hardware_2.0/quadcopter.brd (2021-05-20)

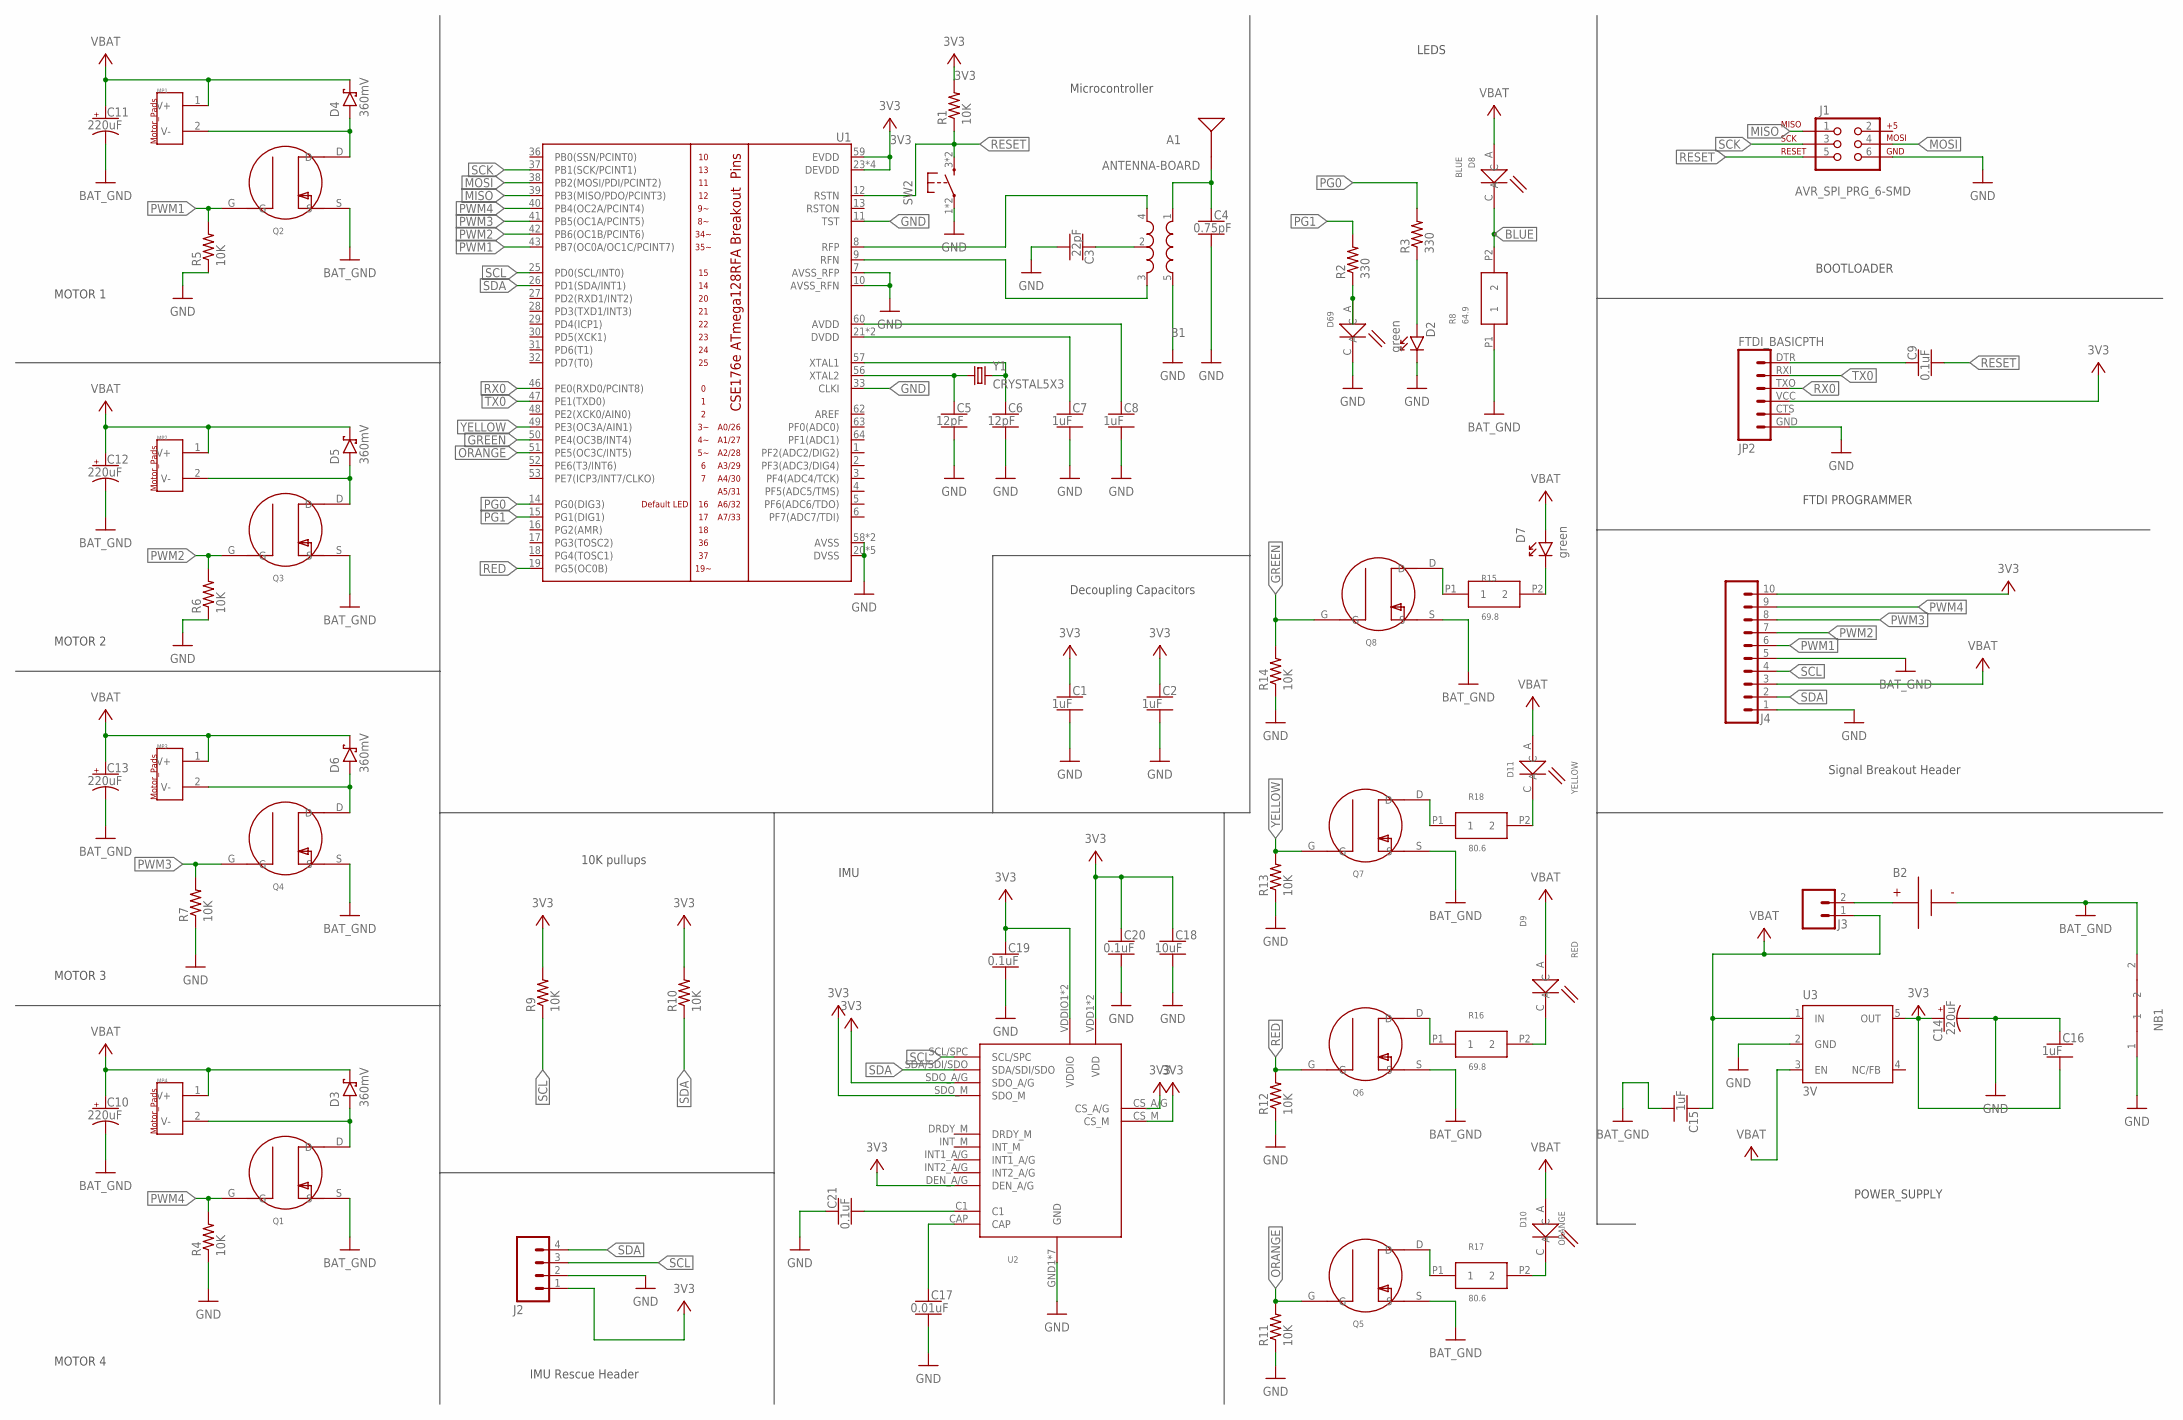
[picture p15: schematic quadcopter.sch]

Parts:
A1: ANTENNA-BOARD; ANT_PCB_2.4GHZ_NRF8001_1.6MM_1OZ
B1: BALUN0805; BALUN
B2: BATTERY-SCREW-TERMINAL; SCREW-TERMINAL-1X2-2.54MM
C1, C2, C7, C8, C15, C16: 1uF; CAPC2012X140_HS
C3: 22pF; CAPC2012X140_HS
C4: 0.75pF; CAPC2012X140_HS
C5, C6: 12pF; CAPC2012X140_HS
C9, C19, C20, C21: 0.1uF; CAPC2012X140_HS
C10, C11, C12, C13, C14: 220uF; CAPMP7343X310_HS
C17: 0.01uF; CAPC2012X140_HS
C18: 10uF; CAPC2012X140_HS
D2, D7: green; LEDSC125X200X120-2_HS
D3, D4, D5, D6: 360mV; SOD3716X135_HS
D8: BLUE; 0805_LED
D9: RED; 0805_LED
D10: ORANGE; 0805_LED
D11: YELLOW; 0805_LED
D69: LEDRED; 0805_LED
J1: AVR_SPI_PRG_6-SMD; 2X3-SMD
J2: HEADER-4POS-0.1IN-FEMALE; HDRVR4W80P254_1X4_1066X254X850B
J3: HEADER-0.1IN-2POS-MALE; HDRV2W63P254_2X1_508X254H838_HS
J4: HEADER-10POSTH-254X10; HDRV10W63P254_10X1_2540X254H838_HS
JP2: FTDI_BASICPTH; FTDI_BASIC
MP1, MP2, MP3, MP4: MOTOR_PADS-MOLEX-0530470210; MOLEX-0530470210
NB1: NETBRIDGE; NET_BRIDGE
Q1, Q2, Q3, Q4, Q5, Q6, Q7, Q8: NMOSFET-NMOSFET; N-CH_MOSFET
R1, R4, R5, R6, R7, R9, R10, R11, R12, R13, R14: 10K; RESC2012X60_HS
R2, R3: 330; RESC2012X60_HS
R8: 64.9; 0805_RESISTOR
R15, R16: 69.8; 0805_RESISTOR
R17, R18: 80.6; 0805_RESISTOR
SW2: PUSHBUTTON_-4.5X4.5; 4.5MM_TACTILE_SWITCH_TL3305AF160QG
U1: ATMEGA128RFA1; QFN-64
U2: LSM9DS1TR9AXISIMU-ACCEL/GYRO/MAGI2C/SPI24LGA; LSM9DS1TR9-AXISIMU
U3: 3V; SOT23-DBV
Y1: CRYSTAL5X3; CRYSTAL-SMD-5X3

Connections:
3V3: C1.1, C2.1, C14.1 (+), C16.2, C18.1, C19.1, C20.1, J2.1, J4.10, JP2.VCC (4), R1.2, R9.2, R10.2, U1.23 (DEVDD), U1.34 (DEVDD), U1.44 (DEVDD), U1.54 (DEVDD), U1.59 (EVDD), U2.CS_A/G, U2.CS_M, U2.DEN_A/G, U2.SDO_A/G, U2.SDO_M, U2.VDD1 (VDD), U2.VDD2 (VDD), U2.VDDIO1 (VDDIO), U2.VDDIO2 (VDDIO), U3.5 (OUT)
A2: B1.4 (OUT1), U1.8 (RFP)
A3: B1.2 (GND), C3.1
A4: B1.3 (OUT2), U1.9 (RFN)
ANT1: A1.FEED, B1.1 (IN), C4.1
BAT_GND: B2.1 (N), C10.2 (-), C11.2 (-), C12.2 (-), C13.2 (-), C15.2, J4.5, NB1.2, Q1.S, Q2.S, Q3.S, Q4.S, Q5.S, Q6.S, Q7.S, Q8.S, R8.P1 (1)
BLUE: D8.C, R8.P2 (2)
GND: B1.5 (GND), C1.2, C2.2, C3.2, C4.2, C5.2, C6.2, C7.2, C8.2, C14.2 (-), C16.1, C17.2, C18.2, C19.2, C20.2, C21.1, D2.C, D69.C, J1.6, J2.2, J4.1, JP2.GND (6), NB1.1, R4.1, R5.1, R6.1, R7.1, R11.1, R12.1, R13.1, R14.1, SW2.1, SW2.2 (1), U1.7 (AVSS_RFP), U1.10 (AVSS_RFN), U1.11 (TST), U1.20 (DVSS), U1.24 (DVSS), U1.33 (CLKI), U1.35 (DVSS), U1.45 (DVSS), U1.55 (DVSS), U1.58 (AVSS), U1.61 (AVSS), U2.GND1 (GND), U2.GND2 (GND), U2.RES1 (GND), U2.RES2 (GND), U2.RES3 (GND), U2.RES4 (GND), U2.RES5 (GND), U3.2 (GND)
GREEN: Q8.G, R14.2, U1.50 (PE4(OC3B/INT4))
MISO: J1.1, U1.39 (PB3(MISO/PDO/PCINT3))
MOSI: J1.4, U1.38 (PB2(MOSI/PDI/PCINT2))
unnamed: C5.1, U1.56 (XTAL2), Y1.1
unnamed: C6.1, U1.57 (XTAL1), Y1.3 (2)
unnamed: D2.A, R3.1
unnamed: B2.2, J3.2
unnamed: C7.1, U1.21 (DVDD), U1.22 (DVDD)
unnamed: C8.1, U1.60 (AVDD)
unnamed: D7.C, R15.P2 (2)
unnamed: Q8.D, R15.P1 (1)
unnamed: Q7.D, R18.P1 (1)
unnamed: D9.C, R16.P2 (2)
unnamed: Q6.D, R16.P1 (1)
unnamed: D10.C, R17.P2 (2)
unnamed: D11.C, R18.P2 (2)
unnamed: Q5.D, R17.P1 (1)
unnamed: D69.A, R2.1
unnamed: C9.1, JP2.DTR (1)
unnamed: D3.A, MP4.2 (V-), Q1.D
unnamed: D4.A, MP1.2 (V-), Q2.D
unnamed: D5.A, MP2.2 (V-), Q3.D
unnamed: C17.1, U2.CAP
unnamed: D6.A, MP3.2 (V-), Q4.D
unnamed: C21.2, U2.C1
ORANGE: Q5.G, R11.2, U1.51 (PE5(OC3C/INT5))
PG0: R3.2, U1.14 (PG0(DIG3))
PG1: R2.2, U1.15 (PG1(DIG1))
PWM1: J4.6, Q2.G, R5.2, U1.43 (PB7(OC0A/OC1C/PCINT7))
PWM2: J4.7, Q3.G, R6.2, U1.42 (PB6(OC1B/PCINT6))
PWM3: J4.8, Q4.G, R7.2, U1.41 (PB5(OC1A/PCINT5))
PWM4: J4.9, Q1.G, R4.2, U1.40 (PB4(OC2A/PCINT4))
RED: Q6.G, R12.2, U1.19 (PG5(OC0B))
RESET: C9.2, J1.5, R1.1, SW2.3 (2), SW2.4 (2), U1.12 (RSTN)
RX0: JP2.TXO (3), U1.46 (PE0(RXD0/PCINT8))
SCK: J1.3, U1.37 (PB1(SCK/PCINT1))
SCL: J2.3, J4.4, R9.1, U1.25 (PD0(SCL/INT0)), U2.SCL/SPC
SDA: J2.4, J4.2, R10.1, U1.26 (PD1(SDA/INT1)), U2.SDA/SDI/SDO
TX0: JP2.RXI (2), U1.47 (PE1(TXD0))
VBAT: C10.1 (+), C11.1 (+), C12.1 (+), C13.1 (+), C15.1, D3.C, D4.C, D5.C, D6.C, D7.A, D8.A, D9.A, D10.A, D11.A, J3.1, J4.3, MP1.1 (V+), MP2.1 (V+), MP3.1 (V+), MP4.1 (V+), U3.1 (IN), U3.3 (EN)
YELLOW: Q7.G, R13.2, U1.49 (PE3(OC3A/AIN1))

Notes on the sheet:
POWER_SUPPLY
Signal Breakout Header
IMU
MOTOR 1
MOTOR 2
MOTOR 3
MOTOR 4
IMU Rescue Header
FTDI PROGRAMMER
BOOTLOADER
LEDS
Microcontroller
10K pullups
Decoupling Capacitors

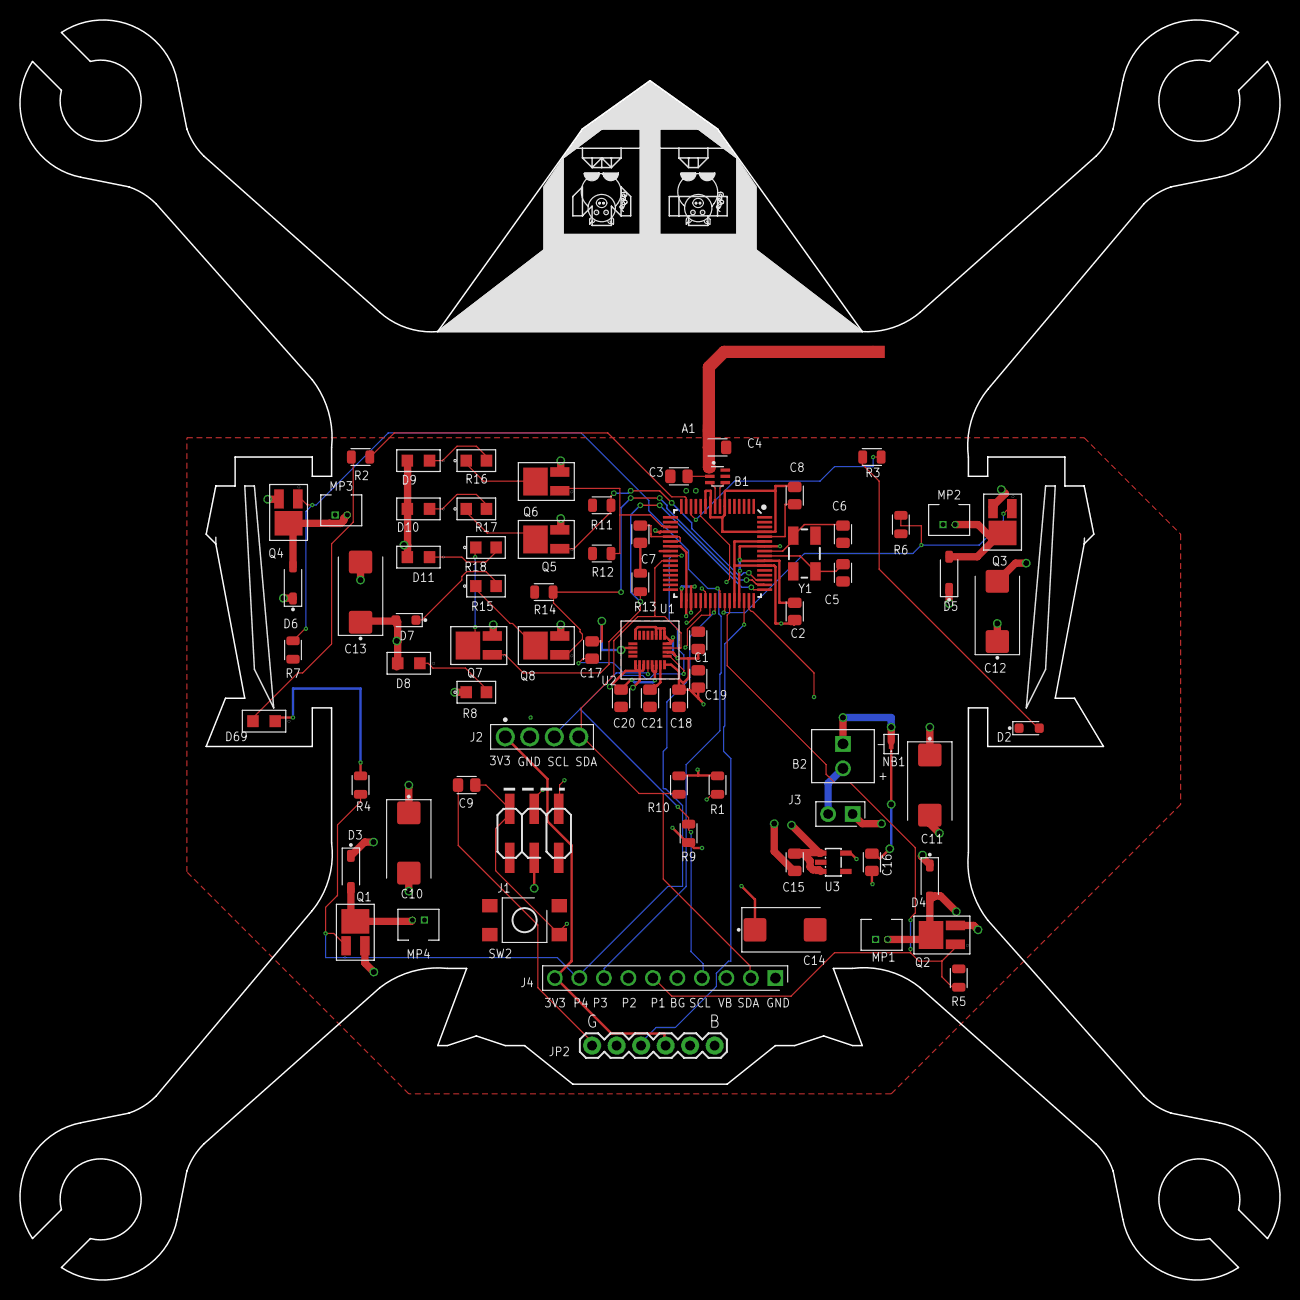
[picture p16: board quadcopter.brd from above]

Board: 4 copper layers, 130.6 x 130.6 mm, 79 parts (0 on the bottom side), 49 nets.

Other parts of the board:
LABELS: LAYER_LABELS
PIG1, PIG2: PIG

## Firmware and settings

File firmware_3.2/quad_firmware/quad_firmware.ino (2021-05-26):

/**
 * @file quad_firmware.ino
 *
 * @mainpage Quadcopter
 *
 * @section description Description
 * The C++ Arduino firmware for a quadcopter made as part of UCSD class CSE 176e
 *
 * @section hardware Hardware
 *  Custom PCB utilizing the ATmega128RFA1.
 * - Quadcopter hardware by Thomas Stuart and Robert Ketchum. Documentation and EAGLE board files available here: https://github.com/rketch/quadcopter
 * - Remote PCB made by UCSD Professor Steven Swanson.
 *
 * @section libraries Libraries
 * All libraries available at: https://github.com/rketch/quadcopter
 * - Wire
 *   - Arduino I2C 
 * - Arduino_LSM9DS1
 *   - Onboard IMU for quadcopter orientation.
 * - Adafruit_Simple_AHRS
 *   - Attitude and heading reference system for LSM
 * - radio
 *   - Radio library. Modified to include data structure sent via radio
 * - quad_remote
 *   - Custom CSE 176e library for the remote
 * - EEPROM
 *   - To save PID and trim calibration values to Non-volatile memory
 * - RotaryEncoder
 *   - To use the knob and button
 *
 *
 * @section authors Authors
 * Created by Thomas Stuart and Robert Ketchum, April 2019.
 * Modified by Robert Ketchum, May 2021.
 *
 */

#include "radio.h"                // Radio library. Modified to include data structure sent via radio
#include <Wire.h>                 // Arduino I2C
#include <Adafruit_Simple_AHRS.h> // Attitude and heading reference system for LSM
#include <Adafruit_LSM9DS1.h>     // Accelerometer/Gyroscope

#define RADIO_CH 17       ///< Radio Channel
#define M1 35             ///< Pin 35 is mapped to motor 1
#define M2 34             ///< Pin 34 is mapped to motor 2
#define M3 8              ///< Pin 8  is mapped to motor 3
#define M4 9              ///< Pin 9  is mapped to motor 4
#define FILT_RATIO 0.91   ///< Complementary filter ratio for a time constant of 10 Hz = 0.91
#define MS_TO_S 1000      ///< Conversion ratio
#define NEUTRAL_PITCH 43  ///< Neutral pitch gimbal position
#define NEUTRAL_ROLL 60   ///< Neutral roll gimbal position
#define NEUTRAL_YAW 60    ///< Neutral yaw gimbal position
#define MAX_ANGLE_FROM_NEUTRAL 10 ///< Maximum pitch or roll from neutral
#define MAX_TRIM_ANGLE 30         ///< Maximum pitch or roll trim angle
#define YAW_MAX_ANG_VEL 60        ///< Maximum yaw angular velocity (deg/sec)
#define TRIM_HISTORY 3            ///< Number of median filtered trim values

/*------------------
 * Section 1:
 * Declare global variables
 * -----------------*/

// Current time and previous step time stamp for controller
unsigned long time;  ///< Current time since start
unsigned int last = millis(); ///< Last loop time since start
double  timeDiff = 0.000000; ///< Implemented in complementary filter and controller


struct Data dataFromRemote; ///< Data structure received over radio

bool resetFlag = false; ///< For zeroing off orientation offset when armed.

// Values needed for the complimentary and median filters
quad_data_t orientation;    ///< Data structure with quadcopter orientation
float accHistoryArr[3][2];  ///< pitch, roll accelerometer reading history
float accHistoryArrCopy[3]; ///< For median filter
float rawGyro[2];           ///< Raw gyro pitch, roll rate
float gyroAngle[2];         ///< Integrated gyro angles
float rawAcc[2];            ///< Raw accelerometer angles
float filteredAngle[2];     ///< Complementary filtered angle
float filtGyroAngle[2];     ///< Partially filtered gyro angle
float filtAccelAngle[2];    ///< Partially filtered accelerometer angle
float gyroAngleStepBack[2]; ///< Previous time step filtered gyroscope angle. Needed for complementary filter
float angleOffset[2];       ///< Accelerometer offset from neutral. Measured when armed.
float trimAngle[2];         ///< Trimm offsets
float trimHistoryArr[3][4]; ///< Pitch, roll trim floats.
float trimHistoryArrCopy[3];///< Trim History for median filter
float medOutTrimArray[4];   ///< Pitch, roll median filter outputs

// PID variables
float   PID_output[3];      ///< PID output
float   remoteSetAngle[3];  ///< Set angle
float   currentAngle[3];    ///< Current quadcopter angle
float   error[3];           ///< Error angle
float   errorSum[3];        ///< Integrated error
float   lastError[3];       ///< previous error (for derivative) 


float MotorValue[4]; ///< Implemented motor thrust variables

/*------------------
 * Section 2:
 * Initialize IMU
 * -----------------*/

.
//  lib file | instance name | constructor in lib file
Adafruit_LSM9DS1 lsm = Adafruit_LSM9DS1(); ///< Create LSM9DS1 board instance
// Create simple AHRS algorithm using the LSM9DS1 instance's accelerometer, gyroscope, and magnetometer.
// lib file     | instance name | instance name for parameter pointers
Adafruit_Simple_AHRS ahrs(&lsm.getAccel(), &lsm.getMag(), &lsm.getGyro());

/** 
 *  set up our instance of the sensor with the wanted register values
 */

void setupLSM(){
    // GYRO [first register]   // Set data rate for G and XL.  Set G low-pass cut off.  (Section 7.12)
    lsm.write8(XGTYPE, Adafruit_LSM9DS1::LSM9DS1_REGISTER_CTRL_REG1_G,  ODR_119 | G_BW_G_11 );

    // Enable the accelerometer X,Y,Z directions (Section 7.23)
    lsm.write8(XGTYPE, Adafruit_LSM9DS1::LSM9DS1_REGISTER_CTRL_REG5_XL, XL_ENABLE_X | XL_ENABLE_Y | XL_ENABLE_Z);
   
    // GYRO [second register]
    lsm.write8(XGTYPE, Adafruit_LSM9DS1::LSM9DS1_REGISTER_CTRL_REG2_G,  G_OUTSEL_HP );
    //lsm.write8(XGTYPE, Adafruit_LSM9DS1::LSM9DS1_REGISTER_CTRL_REG2_G,  G_OUTSEL_RAW ); //0.0 added
  
    // GYRO [third register]
    lsm.write8(XGTYPE, Adafruit_LSM9DS1::LSM9DS1_REGISTER_CTRL_REG3_G, G_HP_CUT_0000 | G_HP_EN ); 

    // Set low-pass XL filter frequency divider (Section 7.25)
    lsm.write8(XGTYPE, Adafruit_LSM9DS1::LSM9DS1_REGISTER_CTRL_REG7_XL, HR_MODE | XL_LP_ODR_RATIO_9 );
    //lsm.write8(XGTYPE, Adafruit_LSM9DS1::LSM9DS1_REGISTER_CTRL_REG7_XL, HR_MODE | XL_LP_ODR_RATIO_50 ); //0.0 replaced
 
    // Magnotometer third register. Enable mag continuous (Section 8.7)
    lsm.write8(MAGTYPE, Adafruit_LSM9DS1::LSM9DS1_REGISTER_CTRL_REG3_M, B00000000);

    // Set up acc, gyro, mag ranges to stop clipping
    lsm.setupAccel(Adafruit_LSM9DS1::LSM9DS1_ACCELRANGE_2G); // 2, 4, 6, 8, or 16 Gs
    lsm.setupMag(Adafruit_LSM9DS1::LSM9DS1_MAGGAIN_4GAUSS);  // 2, 4, 6, 8, or 16 Gauss
    lsm.setupGyro(Adafruit_LSM9DS1::LSM9DS1_GYROSCALE_2000DPS); // 245, 500, or 2000 DPS
}

/*--------------------
 * Section 3:
 * Setup the quadcopter
 * ------------------*/

/**
 * Setup the quadcopter by initializing the radio, motors, IMU registers, and start clock
 */

void setup() {
    //Serial.begin(9600);     // used for consoling out written data
    Serial.begin(115200); // used for reading IMU data on a graph.
    rfBegin(RADIO_CH);      // Initialize radio
    initializeMotors();     // set motors as outputs
    while(!lsm.begin()){    //If no LSM9DS1 detected, send error message to user
        Serial.println(F("Ooops, no LSM9DS1 detected ... Check your wiring or I2C address!"));
        delay(1000);
        }
    setupLSM();   // Setup LSM. Helps with noise over defulat option.
    time = millis();             // start clock
    //dataFromRemote.arm = 0;    // if Reset is hit, restart
    resetFlag = true;            // Prevent motors from spinning on reset
    }

/*------------------
 * Section 4:
 * Loop forever
 * -----------------*/

/**
 * Loop forever. Receive radio data, find current quadcopter orientation, compute control system values, 
 * find current throttle corrections,write throttle values to motors if armed.
 */

void loop() {
    unsigned int now = millis();
    timeDiff = float(now - last)/1000;  // update time in seconds
    verifyRadioData();                  // receive and verify radio data 
    ComplimentaryFilter(timeDiff);      // Find the current quad angle
    PID(timeDiff);                      // Call the controller function
    mixer();                            // MIX the user throttle values with the controller offsets
    if ((dataFromRemote.arm == 1)&&(resetFlag == true)){       // if just armed quad, zero accelerometer
        calibrateAccelerometer();       // Zero Accelerometer
        resetFlag = false;
        }
    else if ((dataFromRemote.arm == 1)&&(resetFlag == false)){ // If armed, write command to motor
        engageMotors();  // run motors
        }
    else{                                                      // if disarmed, shut down motors 
        disableMotors(); // prevent motors from running
        }
    last = now;                       //update the time step
    }

/*---------------------------
 * Section 5:
 * Verify Received Radio Data
 * -------------------------*/

/**
* Read radio data received from the remote. If it is verified, save the data in a structure
*/

void verifyRadioData(){
    uint8_t buff[256];
    int len;
    if (len = rfAvailable()){                // If the quad receives radio signal from the controller
        rfRead(buff, len);                   // read the data sent, save buffer as "buff", length as "len"
        if(  (buff[54] == 154) && (buff[55] == 2) && (len == 126) ){  // Radio data checksum.
            dataFromRemote = *(Data*)buff;   // save the received data as a new instance
            }
        }
    }

/*------------------------------
 * Section 6:
 * Complementary Filter Function
 * ----------------------------*/

/**
* Combine the gyroscope and accelerometer to get an accurate heading of the quadcopter
* @param  dt The time difference between calling the function (in ms)
*/

void ComplimentaryFilter( double dt ){
    if (ahrs.getQuadOrientation(&orientation) ){  // if we have a new valid sensor reading
      // /*activate median filter for accelerometer readings
        for (int j=0; j<2; j++){ // for pitch, roll
            for (int i=0; i<2; i++){ // update acc steps
                accHistoryArr[i][j] = accHistoryArr[i+1][j];
                }
            accHistoryArr[2][0] = orientation.pitch; // get new acc reading
            accHistoryArr[2][1] = orientation.roll;  // get new acc reading
            }
        for (int i=0; i<2; i++){                     // for pitch, roll
            for (int j=0; j<3;j++){                  // make copies of the previous steps to send to median filter
                accHistoryArrCopy[j] = accHistoryArr[j][i];
                }
            rawAcc[i] = median(accHistoryArrCopy, 3);
            }
        // */ end median filter for accelerometer readings
        //rawAcc[0] = orientation.pitch;     // to use raw readings instead of median
        //rawAcc[1] = orientation.roll;      // to use raw readings instead of median
        rawGyro[0] = orientation.pitch_rate; // raw gyroscope angular velocity
        rawGyro[1] = orientation.roll_rate;  // raw gyroscope angular velocity
        for (int i=0; i<2; i++){             // for pitch, roll
            gyroAngleStepBack[i] = gyroAngle[i];         // previous gyro value for high pass filter
            gyroAngle[i] = gyroAngle[i] + rawGyro[i]*dt; // Integrate raw gyro value
            filtGyroAngle[i] = FILT_RATIO * (filtGyroAngle[i] + gyroAngle[i] - gyroAngleStepBack[i]); // high pass the gyroscope reading
            filtAccelAngle[i] = FILT_RATIO * filtAccelAngle[i] + (1 - FILT_RATIO) * rawAcc[i];        // low pass the accelerometer reading
            filteredAngle[i] = filtGyroAngle[i] + filtAccelAngle[i];                                  // complementary filter output
            }
        }
    }

/*------------------------------
 * Section 7:
 * PID Controller Function
 * ----------------------------*/

/**
* Utilize PID controller to ensure stable quadcopter flight
* @param  dt The time difference between calling the function (in ms)
*/

void PID(double dt ){
    findGimbalOffsets(); // Find the remote set angles from the gimbal positions
    findTrimOffsets();   // Find current trim values
    //current angle is obtained by reading the on board orientation data and subtracting off the trim and offset
    currentAngle[0] = -filteredAngle[0] - angleOffset[0] - trimAngle[0]; // pitch
    currentAngle[1] = -filteredAngle[1] - angleOffset[1] - trimAngle[1]; // roll
    currentAngle[2] = -orientation.yaw_rate;                             // yaw rate (unfiltered)
    //  i = 0 ( pitch )  , i = 1 ( roll ) , i = 2 ( yaw )   
    for( int i = 0; i < 3; i++){                                    // For Pitch, Roll, Yaw
        error[i] = remoteSetAngle[i] - currentAngle[i];             // Current Error
        errorSum[i] = errorSum[i] + error[i];                       // Integrated Error
        Coefficients k =   dataFromRemote.coefficientsContainer[i]; // Load Pitch, Yaw, or Roll PID values
        PID_output[i] = (k.proportional * error[i] ) + (k.integral * ( errorSum[i] * dt ) ) + ( k.derivative * ( (error[i] - lastError[i])/dt) );
        //               Proportional                    Integral                              Derivative
        lastError[i] = error[i];                                    // For error derivative
        }
    }

/*------------------------------
 * Section 8:
 * Function findGimbalOffsets
 * ----------------------------*/

/**
* Find the remote set angles from the gimbal positions
*/

void findGimbalOffsets(){
    //PITCH
    if (dataFromRemote.pitch > NEUTRAL_PITCH * 2){ // limit gimbal reading to accurate values
        dataFromRemote.pitch = NEUTRAL_PITCH * 2;
        }
    remoteSetAngle[0]     = float(dataFromRemote.pitch) * (MAX_ANGLE_FROM_NEUTRAL * 2) / (NEUTRAL_PITCH * 2) - MAX_ANGLE_FROM_NEUTRAL;
    //ROLL
    if (dataFromRemote.roll > NEUTRAL_ROLL * 2){ // limit gimbal reading to accurate values
        dataFromRemote.roll = NEUTRAL_ROLL * 2;
        }
    remoteSetAngle[1]     = -float(dataFromRemote.roll) * (MAX_ANGLE_FROM_NEUTRAL * 2) / (NEUTRAL_ROLL * 2) + MAX_ANGLE_FROM_NEUTRAL;
    //YAW
    if (dataFromRemote.yaw > NEUTRAL_YAW * 2){ // limit gimbal reading to accurate values
        dataFromRemote.yaw = NEUTRAL_YAW * 2;
        }
    remoteSetAngle[2]     = 2*(float(dataFromRemote.yaw) - YAW_MAX_ANG_VEL);
    }

/*------------------------------
 * Section 9:
 * Function findTrimOffsets
 * ----------------------------*/

/**
* Median the trim data and convert to a float angle.
*/

void findTrimOffsets(){
    if(dataFromRemote.pitchTrimSign){ // if negative
        trimAngle[0] = -float(dataFromRemote.pitchTrimMagnitude) * float(MAX_TRIM_ANGLE) / 255;
        }
    else{                   // if positive
        trimAngle[0] = float(dataFromRemote.pitchTrimMagnitude) * float(MAX_TRIM_ANGLE) / 255;
        }
    if(dataFromRemote.rollTrimSign){ // if negative
        trimAngle[1] = -float(dataFromRemote.rollTrimMagnitude) * float(MAX_TRIM_ANGLE) / 255;
        }
    else{                   // if positive
        trimAngle[1] = float(dataFromRemote.rollTrimMagnitude) * float(MAX_TRIM_ANGLE) / 255;
        }
    }

/*------------------------------
 * Section 10:
 * Median Filter Function
 * ----------------------------*/

/**
* Find the middle value of three raw inputs to filter out pertubations. Thanks geeksforgeeks
* @param  medArray An array containing the last n sensed values
* @param  n The length of medArray
* @return The median value
*/

float median(float medArray[], int n){
     sort(medArray, n);
     if (n % 2 != 0){ // if an odd number of values in array
         return (float)medArray[n / 2];
         }
     else{ // if an even number
         return (float)(medArray[(n - 1) / 2] + medArray[n / 2]) / 2.0;
         }
    }

/*------------------------------
 * Section 11:
 * Sort Array Function
 * ----------------------------*/

/**
* Sort an array into increasing numerical values. Thanks tsbrownie on youtube.
* @param unsortedArray An array containing the last n sensed values
* @param n The length of medianFinder
*/

void sort(float unsortedArray[], int n){
    for(int x = 0; x < n; x++){
        for(int y = 0; y < n-1; y++){
            if(unsortedArray[y] > unsortedArray[y+1]){
                float tempVal = unsortedArray[y+1];
                unsortedArray[y+1] = unsortedArray[y];
                unsortedArray[y] = tempVal;
                }
            }
        }
    }

/*------------------------------
 * Section 12:
 * Calibrate Accelerometer Funciton
 * ----------------------------*/

/**
* Calculate the angle offset of the accelerometer
*/

void calibrateAccelerometer(){
    for (int i=0; i<2; i++){ // pitch, roll
        angleOffset[i] = -filteredAngle[i];
        }
    }

/*------------------------------
 * Section 13:
 * Throttle Mixing Function
 * ----------------------------*/

/**
* Mix the user throttle value and the PID controller output
*/

void mixer(){
    if(dataFromRemote.throt <= 1){ // if throttle is off
        for (int i=0; i<4; i++){   // Don't spin motor
            MotorValue[i] = 0;
            }
        for (int i; i<3; i++){     // Reset Integral Error
            errorSum[i] = 0;
            }
        }
    else{
        //  i = 0 ( pitch )  , i = 1 ( roll ) , i = 2 ( yaw ) 
        MotorValue[0] = (float)dataFromRemote.throt + PID_output[0] - PID_output[1] + PID_output[2]; // front starboard
        MotorValue[3] = (float)dataFromRemote.throt + PID_output[0] + PID_output[1] - PID_output[2]; // front port
        MotorValue[1] = (float)dataFromRemote.throt - PID_output[0] - PID_output[1] - PID_output[2]; // back starboard
        MotorValue[2] = (float)dataFromRemote.throt - PID_output[0] + PID_output[1] + PID_output[2]; // back port
        }
    for (int i=0; i<4; i++){ // Prevent motor values from exceeding PWM limits
        if (MotorValue[i] < 0){
            MotorValue[i] = 0;
            }
        if (MotorValue[i] > 255){
            MotorValue[i] = 255;
            }
        }
    }

/*------------------------------
 * Section 14:
 * Initialize Motors Function
 * ----------------------------*/

/**
* Initialize motor pins
*/

void initializeMotors(){
    pinMode(M1, OUTPUT); 
    pinMode(M2, OUTPUT);
    pinMode(M3, OUTPUT);
    pinMode(M4, OUTPUT);
    pinMode(LED_BUILTIN,OUTPUT);
    }

/*------------------------------
 * Section 15:
 * Disable Motors Function
 * ----------------------------*/

/**
* Ensure that the motors do not run when the quad is disarmed
*/

void disableMotors(){
    digitalWrite(LED_BUILTIN,LOW);
    analogWrite(M1, 0);
    analogWrite(M2, 0);
    analogWrite(M3, 0);
    analogWrite(M4, 0);
    }

/*------------------------------
 * Section 14:
 * Engage Motors Function
 * ----------------------------*/

/**
* Write the motor commands to the respective motors
*/

void engageMotors(){
    digitalWrite(LED_BUILTIN,HIGH);
    analogWrite(M1, MotorValue[1]);      // back starboard
    analogWrite(M2, MotorValue[0]);      // front starboard
    analogWrite(M3, MotorValue[3]);      // front port
    analogWrite(M4, MotorValue[2]);      // back port
    }

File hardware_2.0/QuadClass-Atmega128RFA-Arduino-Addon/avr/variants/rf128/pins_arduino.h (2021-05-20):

/*
  pins_arduino.h - Pin definition functions for Arduino
  Part of Arduino - http://www.arduino.cc/

  Copyright (c) 2007 David A. Mellis

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
  $Id: wiring.h 249 2007-02-03 16:52:51Z mellis $
*/

/*
	This version of pins_arduino.h is for the Zigduino r1
	Pierce Nichols 2011 Oct 11
	Amended for the SparkFun ATmega128RFA1 -- Jim Lindblom 2013 Jun 29
	Amended for the UCSD Quadcopter class -- Steven Swanson 2018 Jun 22
*/

#ifndef Pins_Arduino_h
#define Pins_Arduino_h

#include <avr/pgmspace.h>

#define NUM_DIGITAL_PINS            29
#define NUM_ANALOG_INPUTS           8
#define analogInputToDigitalPin(p)  ((p < NUM_ANALOG_INPUTS) ? (p) + 26 : -1)
#define digitalPinHasPWM(p)         ((p) == 3 ||(p) == 4 ||(p) == 5 ||(p) == 8 ||(p) == 9 ||(p) == 19 ||(p) == 34 || (p) == 35)

const static uint8_t SS   = 10;
const static uint8_t MOSI = 11;
const static uint8_t MISO = 12;
const static uint8_t SCK  = 13; 

const static uint8_t SDA = 14;
const static uint8_t SCL = 15;
const static uint8_t LED = 16;
const static uint8_t LED_BUILTIN = 16;
const static uint8_t LED1 = 16;
const static uint8_t LED2 = 17;

#if(0)
const static uint8_t A0 = 26;
const static uint8_t A1 = 27;
const static uint8_t A2 = 28;
const static uint8_t A3 = 29;
const static uint8_t A4 = 30;
const static uint8_t A5 = 31;
const static uint8_t A6 = 32;
const static uint8_t A7 = 33;
#endif

const static uint8_t A0 = 0; // 26
const static uint8_t A1 = 1; // 27
const static uint8_t A2 = 2; // 28
const static uint8_t A3 = 3; // 29
const static uint8_t A4 = 4; // 30
const static uint8_t A5 = 5; // 31
const static uint8_t A6 = 6; // 32
const static uint8_t A7 = 7; // 33

// A majority of the pins are NOT PCINTs, SO BE WARNED (i.e. you cannot use them as receive pins)
// Only pins available for RECEIVE (TRANSMIT can be on any pin):
// Pins: 7, 8, 9, 10, 11, 12, 13, 20

#define digitalPinToPCICR(p)    ( (((p) >= 7) && ((p) <= 13)) || \
                                  ((p) == 20) ? (&PCICR) : ((uint8_t *)0) )

#define digitalPinToPCICRbit(p) ( ((p) == 7) ? 1 : 0 ) 

#define digitalPinToPCMSK(p)    ( ((((p) >= 8) && ((p) <= 13)) || ((p) == 20)) ? (&PCMSK0) : \
                                ( ((p) == 7) ? (&PCMSK1) : \
				  ((uint8_t *)0) ) )

#define digitalPinToPCMSKbit(p) ( ((p) == 7) ? 0 : \
                                ( ((p) == 8) ? 4 : \
                                ( ((p) == 9) ? 7 : \
                                ( ((p) == 10) ? 6 : \
                                ( ((p) == 11) ? 5 : \
                                ( ((p) == 12) ? 3 : \
                                ( ((p) == 13) ? 1 : \
                                ( ((p) == 20) ? 2 : \
				  0 ) ) ) ) ) )))

#ifdef ARDUINO_MAIN

const uint16_t PROGMEM port_to_mode_PGM[] = {
	NOT_A_PORT,
	NOT_A_PORT,
	(uint16_t)&DDRB,
	NOT_A_PORT,
	(uint16_t)&DDRD,
	(uint16_t)&DDRE,
	(uint16_t)&DDRF,
	(uint16_t)&DDRG,
	NOT_A_PORT,
	NOT_A_PORT,
	NOT_A_PORT,
	NOT_A_PORT,
	NOT_A_PORT,
};

const uint16_t PROGMEM port_to_output_PGM[] = {
	NOT_A_PORT,
	NOT_A_PORT,
	(uint16_t)&PORTB,
	NOT_A_PORT,
	(uint16_t)&PORTD,
	(uint16_t)&PORTE,
	(uint16_t)&PORTF,
	(uint16_t)&PORTG,
	NOT_A_PORT,
	NOT_A_PORT,
	NOT_A_PORT,
	NOT_A_PORT,
	NOT_A_PORT,
};

const uint16_t PROGMEM port_to_input_PGM[] = {
	NOT_A_PIN,
	NOT_A_PIN,
	(uint16_t)&PINB,
	NOT_A_PIN,
	(uint16_t)&PIND,
	(uint16_t)&PINE,
	(uint16_t)&PINF,
	(uint16_t)&PING,
	NOT_A_PIN,
	NOT_A_PIN,
	NOT_A_PIN,
	NOT_A_PIN,
	NOT_A_PIN,
};

const uint8_t PROGMEM digital_pin_to_port_PGM[] = {
	// PORTLIST		
	// -------------------------------------------		
	PE	, // PE 0 ** 0 ** D0 / USART0_RX	
	PE	, // PE 1 ** 1 ** D1 / USART0_TX	
	PE	, // PE 2 ** 2 ** D2
	PE	, // PE 3 ** 3 ** D3 / PWM
	PE	, // PE 4 ** 4 ** D4 / PWM
	PE	, // PE 5 ** 5 ** D5 / PWM
	PE	, // PE 6 ** 6 ** D6
	PE	, // PE 7 ** 7 ** D7

	PB	, // PB 5 ** 8 ** D8 / PWM
	PB	, // PB 4 ** 9 ** D9 / PWM
	PB	, // PB 0 ** 10 ** D10 / SPI_SSN
	PB	, // PB 2 ** 11 ** D11 / SPI_MOSI
	PB	, // PB 3 ** 12 ** D12 / SPI_MISO
	PB	, // PB 1 ** 13 ** D13 / SPI_SCK

	PD	, // PD 1 ** 14 ** D14 / I2C_SDA
	PD	, // PD 0 ** 15 ** D15 / I2C_SCL

	PG	, // PG 0 ** 16 ** D16 / LED1 / LED
	PG	, // PG 1 ** 17 ** D17 / LED2 
	PG	, // PG 2 ** 18 ** D18
	PG	, // PG 5 ** 19 ** D19 / PWM

	PD	, // PD 2 ** 20 ** D20 / USART1_RX
	PD	, // PD 3 ** 21 ** D21 / USART1_TX
	PD	, // PD 4 ** 22 ** D22
	PD	, // PD 5 ** 23 ** D23
	PD	, // PD 6 ** 24 ** D24
	PD	, // PD 7 ** 25 ** D25

	PF	, // PF 0 ** 26 ** A0 / D26
	PF	, // PF 1 ** 27 ** A1 / D27
	PF	, // PF 2 ** 28 ** A2 / D28
	PF	, // PF 3 ** 29 ** A3 / D29
	PF	, // PF 4 ** 30 ** A4 / D30	
	PF	, // PF 5 ** 31 ** A5 / D31	
	PF	, // PF 6 ** 32 ** A6 / D32	
	PF	, // PF 7 ** 33 ** A7 / D33

	PB	, // PB 6 ** 34 ** D34 / PWM
	PB	, // PB 7 ** 35 ** D35 / PWM

	PG	, // PG 3 ** 36 ** D36 
	PG	, // PG 4 ** 37 ** D37 
};
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

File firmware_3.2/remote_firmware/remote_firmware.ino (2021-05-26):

#include "quad_remote.h"   // Custom CSE 176e library for the remote
#include "radio.h"         // Radio library. Modified to include data structure sent via radio
#include <EEPROM.h>        // To save PID and trim calibration values to Non-volatile memory
#include <RotaryEncoder.h> // To use the knob and button

#define RADIO_CH 17 ///< Radio Channel
#define MAX_TRIM_ANGLE 30 ///< Maximum trim angle
#define TRIM_INCREMENT 10 ///< Increment by which trim is changed on remote

/*------------------
 * Section 1:
 * Declare global variables
 * -----------------*/

struct Data remoteToQuadData; ///< Structure for radio data. Struct "Data" initialized in radio.h

// Raw gimbal values. Organized as:
// [0] = A2 = pitch; [1] = A3 = roll; [2] = A1 = yaw; [3] = A0 = throt 
int gimbalRawValues[4];  ///< Values read by gimbal. Nominally 0 - 1024 but constrained by the potentiometer
int lowestGimbalValueReadSoFar[4]   = {  0,   0,   0,   0}; ///< lowest value possible by analog stick gimbal
int largestGimbalValueReadSoFar[4]  = {303, 318, 320, 306}; ///< highest value possible by analog stick gimbal
int saveLargestGimbalValuesSoFar[12]; ///< 255 + 255 + 255 = 765 is the highest save value with EEPROM for gimbal

// Values for rotary knob and its button
void knobPressed(bool); // Keeps track of the knob button
void knobsUpdate(); // Keeps track of the rotary knob value
bool knob_btn = 0; ///< Whether the knob button is pressed

// States of the remote
bool armToken = true;  ///< State variable for armed mode
bool isInTrimMode = false; ///< State variable for trim mode

// Variables for PID tuning and displaying values over LCD screen
int  cpa [3][6]; ///< Coefficients Properties Array for displaying and storing PID coefficients for pitch, yaw, roll. 3 rows, 6 columns
int  sign[9] = {1,1,1,  1,1,1,  1,1,1};  ///< Sign of PID tuning coefficients for storing via EEPROM
int  PIDpos = 0; ///< PID value being tuned currently
bool changeLeft = 1; ///< Keeps track of whether we are tuning whole integer or decimal PID value
int row = 0;  ///< LCD screen row to write to
int col = 0;  ///< LCD screen column to write to
int calculateColPos(int , bool  );
float trimAngle[2]; ///< Trim pitch and roll angles
String top = ""; ///< Initialize string to print on top row of LCD screen for PID tuning
int colPosStart[3]; ///< What column we are writing to LCD screen for PID tuning
bool knob_token = false; ///< trim or PID tuning variable
void updateDisplayPIDElementChange();

//Variables for converting integers to decimal. Integers may be saved on EEPROM, while float values are sent over radio.
void converToDecimalsBeforeSend();
float castIntPairToDecimal( int, int);

// Variables and function declarations for reading and writing to EEPROM.
void readPIDArrayFromEeprom(int);
void writePIDToEeprom();  // send current PID values to EEPROM
void writeGimbalsToEeprom(); // send calibrated gimbal values to EEPROM
int timesOverflowed = 0; ///< Keeps track of times an integer has overflowed for EEPROM writing

/*------------------
 * Section 2:
 * Set up remote
 * -----------------*/

/**
 * Setup the remote firmware by initializing radio, gimbal pins, LCD screen, 
 * knobs and buttons, and reading PID and trim values from EEPROM.
 */

void setup() {
    Serial.begin(9600);              // set up serial
    rfBegin(RADIO_CH);               // initialize radio on channel 17
    quad_remote_setup();             // initialize gimbal pins, lcd screen
    remoteToQuadData.arm = 0;        // to disable and enable throttle values to be reflected on quad.
    armToken = true;                 // every time the code resets, allow the arm symbol "A" to be displayed on remote
    isInTrimMode = false;            // start the remote in PID control tuning mode
    knob1_btn_cb = knobPressed;      // Initialize callback to check if knob being pressed
    knobs_update_cb = knobsUpdate;   // Initialize callback to check if knob value being changed
    knobsUpdate();                   // initialize knob
    initializeButtonPins();          // initialize buttons
    eepromRead();                    // read stored EEPROM calibration and PID values
    updateDisplayPIDElementChange(); // initialize LCD screen to PID tuning
    }

/*------------------
 * Section 3:
 * Loop
 * -----------------*/

/**
 * Loop endlessly. Read gimbal positions, determine if quadcopter should be armed, 
 * determine which LCD tuning state the remote should be in, determine whether the user is inputing commands, and
 * send data structure to quadcopter over radio.
 */

void loop() {
    readAndMapGimbals();            // Read raw gimbal values
    isInArmState(remoteToQuadData); // Are we arming the quadcopter right now?
    if (isInTrimMode){              // Trim state variable
      TrimTuningState();            // Display trim tuning on remote screen
    }
    else{
      PIDTuningState();             // Display PID tuning on remote screen.
    }
    converToDecimalsBeforeSend();   // Convert from integer values displayed on LCD to floats to send over radio
    rfSend(remoteToQuadData);       // send data over radio
    }

/*----------------------------
 * Section 4:
 * Function PIDTuningState
 * --------------------------*/

/**
* This function serves as a state machine. It is called when the remote is in the PID editing state
*/
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

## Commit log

2021-05-26 add BOM
2021-07-21 Added Kalman Filter

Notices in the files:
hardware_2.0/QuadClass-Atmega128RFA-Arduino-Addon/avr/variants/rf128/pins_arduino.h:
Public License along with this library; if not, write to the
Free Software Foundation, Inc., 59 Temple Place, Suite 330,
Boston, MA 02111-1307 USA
